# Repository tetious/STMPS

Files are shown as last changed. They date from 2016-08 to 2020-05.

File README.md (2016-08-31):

STMPS
=====

**STMPS** is a WIP 3d printer board based around the STM32f411, with inspiration and guidance
from the Printrboard, RAMPS 1.4, and the RepRap project.

**ALPHA-3**

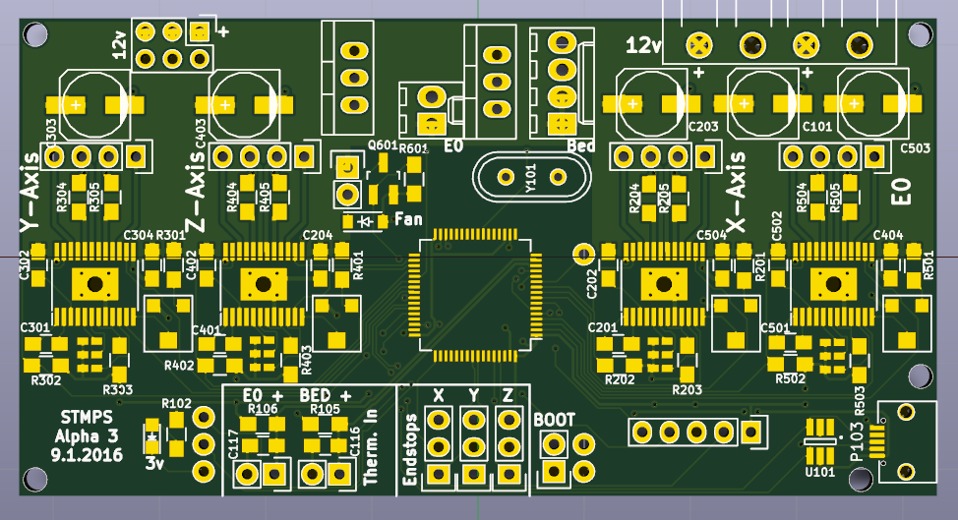
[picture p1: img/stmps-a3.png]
a3


This board is intended to work with Ambroz Bizjak's astonishingly fantastic 
[aprinter](https://github.com/ambrop72/aprinter) firmware. Configuration files and guidance will be
provided once the board is further along.

STMPS is open source hardware, licensed under CC BY-SA. Copyright (C) 2016 Greg Lincoln.

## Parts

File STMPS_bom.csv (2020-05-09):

Component | Description | Part | References | Value | Footprint | Quantity Per PCB | Datasheet | MPN
1 | Unpolarized capacitor | C_Small | C108 C110 C111 C112 C201 C202 C204 C301 C302 C304 C401 C402 C404 C501 C502 C504 | 100nf | C_0805_HandSoldering | 16
2 | Polarised capacitor | CP_Small | C101 | 100uf | c_elec_6.3x5.8 | 1 |  | 35TZV100M6.3X8
3 | Polarised capacitor | CP1_Small | C203 C303 C403 C503 | 100uf | c_elec_6.3x5.8 | 4 |  | UWT1V101MCL1GS
4 | Unpolarized capacitor | C_Small | C102 C116 C117 | 10uf | C_0805_HandSoldering | 3
5 | Unpolarized capacitor | C_Small | C103 C104 | 20pf | C_0805_HandSoldering | 2
6 | Unpolarized capacitor | C_Small | C113 C114 | 4.7uf | C_0805_HandSoldering | 2
7 | LED, small symbol | LED_Small | D101 | 12v_PWR | LED_0805 | 1
8 | LED, small symbol | LED_Small | D102 | 3v_PWR | LED_0805 | 1
9 | Schottky diode, small symbol | D_Schottky_Small | D103 D601 | D_Schottky_Small | SOD-123 | 2 |  | DB2X41100L DB2J41100L
10 | LED, small symbol | LED_Small | D701 D801 | r | LED_0805 | 2
11 | Connector, single row, 01x02, pin header | CONN_01X02 | JP101 | BOOT0 | Pin_Header_Straight_1x02 | 1
12 | Jumper, normally closed | Jumper_NC_Small | JP203 JP303 JP403 JP503 | MS1 | MADW__SMD-solder-bridge-narrow | 4
13 | Jumper, normally closed | Jumper_NC_Small | JP202 JP302 JP402 JP502 | MS2 | MADW__SMD-solder-bridge-narrow | 4
14 | Jumper, normally closed | Jumper_NC_Small | JP201 JP301 JP401 JP501 | MS3 | MADW__SMD-solder-bridge-narrow | 4
15 | Connector, double row, 02x03, pin header | CONN_02X03 | P102 | 12v | Pin_Header_Straight_2x03 | 1
16 | Connector, single row, 01x04, pin header | CONN_01X04 | P101 | 12v IN | 5EHDRC_1x04 | 1
17 | Connector, single row, 01x04, pin header | CONN_01X04 | P110 | BED | Molex_KK-6410-04_04x2.54mm_Straight | 1
18 | Connector, single row, 01x02, pin header | CONN_01X02 | P107 | BED_THERM | Pin_Header_Straight_1x02 | 1
19 | Connector, single row, 01x02, pin header | CONN_01X02 | P104 | E0_THERM | Pin_Header_Straight_1x02 | 1
20 | Connector, single row, 01x02, pin header | CONN_01X02 | P111 | EO | Molex_KK-6410-02_02x2.54mm_Straight | 1
21 | Connector, single row, 01x02, pin header | CONN_01X02 | P601 | LP_OUT | Pin_Header_Straight_1x02 | 1
22 | Connector, single row, 01x04, pin header | CONN_01X04 | P201 P301 P401 P501 | MOT | Pin_Header_Straight_1x04 | 4
23 | Connector, single row, 01x05, pin header | CONN_01X05 | P106 | SWD | Pin_Header_Straight_1x05 | 1
24 | USB mini/micro connector | USB_OTG | P103 | USB_OTG | USB_Micro-B-ebay | 1
25 | Connector, single row, 01x03, pin header | CONN_01X03 | P105 | X_STOP | Pin_Header_Straight_1x03 | 1
26 | Connector, single row, 01x03, pin header | CONN_01X03 | P108 | Y_STOP | Pin_Header_Straight_1x03 | 1
27 | Connector, single row, 01x03, pin header | CONN_01X03 | P109 | Z_STOP | Pin_Header_Straight_1x03 | 1
28 | Transistor N-MOSFET with substrate diode (general) | Q_NMOS_GDS | Q701 Q801 | IPP039N04L | TO-220_Neutral123_Vertical | 2 |  | IPP039N04LGXKSA1-ND
29 | Transistor N-MOSFETwith substrate diode (general) | Q_NMOS_GSD | Q601 | SSM3K333 | SOT-23_Handsoldering | 1 |  | SSM3K333RLFCT-ND
30 | Resistor, small symbol | R_Small | R204 R205 R304 R305 R404 R405 R504 R505 | 0.1 | R_0805_HandSoldering | 8
31 | Resistor, small symbol | R_Small | R702 R802 | 100 | R_0805_HandSoldering | 2
32 | Resistor, small symbol | R_Small | R104 R202 R203 R302 R303 R402 R403 R502 R503 R601 R701 R801 | 100k | R_0805_HandSoldering | 12
33 | Resistor, small symbol | R_Small | R201 R301 R401 R501 | 200k | R_0805_HandSoldering | 4
34 | Resistor, small symbol | R_Small | R103 | 220 | R_0805_HandSoldering | 1
35 | Resistor, small symbol | R_Small | R105 R106 R107 | 4.7k | R_0805_HandSoldering | 3
36 | Resistor, small symbol | R_Small | R102 | 56 | R_0805_HandSoldering | 1
37 | Resistor, small symbol | R_Small | R101 R703 R803 | 560 | R_0805_HandSoldering | 3
38 | Potentionmeter | POT | RV201 RV301 RV401 RV501 | 100k | BOURNS-TC33X-2 | 4 |  | TC33X-2-104E
39 |  | A5984 | U201 U301 U401 U501 | A5984 | TSSOP-24_4.4x7.8mm_Pitch0.65mm | 4 |  | A5984GLPTR-T
40 |  | AOZ8904 | U101 | AOZ8904 | SOT-23-6_Handsoldering | 1 |  | AOZ8904CIL
41 |  | CHIP-TOP | U105 | CHIP-TOP | CHIP-MIN | 1
42 |  | LM1117 | U102 | LM1117-3.3v | TO-252-2Lead | 1
43 |  | STM32F411RCTx | U103 | STM32F411RCTx | LQFP-64_10x10mm_Pitch0.5mm | 1 |  | STM32F411RCT6
44 | Two pin crystal, small symbol | Crystal_Small | Y101 | Crystal | Crystal_HC49-U_Vertical | 1 |  | ABL-8.000MHZ-B2
Component Groups: | 44
Component Count: | 113
Fitted Components: | 113
Number of PCBs: | 1
Total components: | 113
Schematic Version:
Schematic Date:
BoM Date: | Thu 20 Jul 2017 09:48:18 PM EDT
Schematic Source: | /home/greg/Boards/STMPS/STMPS.sch
KiCad Version: | Eeschema 4.0.7-e0-6372~58~ubuntu16.04.1

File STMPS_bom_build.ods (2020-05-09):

Part | References | Value | MPN
C_Small | C108 C110 C111 C112 C201 C202 C204 C301 C302 C304 C401 C402 C404 C501 C502 C504 | 100nf
CP_Small | C101 | 100uf | 35TZV100M6.3X8
CP1_Small | C203 C303 C403 C503 | 100uf | UWT1V101MCL1GS
C_Small | C102 C116 C117 | 10uf
C_Small | C103 C104 | 20pf
C_Small | C113 C114 | 4.7uf
LED_Small | D101 | 12v_PWR
LED_Small | D102 | 3v_PWR
D_Schottky_Small | D103 D601 | D_Schottky_Small | DB2X41100L DB2J41100L
LED_Small | D701 D801 | r
CONN_01X02 | JP101 | BOOT0
Jumper_NC_Small | JP203 JP303 JP403 JP503 | MS1
Jumper_NC_Small | JP202 JP302 JP402 JP502 | MS2
Jumper_NC_Small | JP201 JP301 JP401 JP501 | MS3
CONN_02X03 | P102 | 12v
CONN_01X04 | P101 | 12v IN
CONN_01X04 | P110 | BED
CONN_01X02 | P107 | BED_THERM
CONN_01X02 | P104 | E0_THERM
CONN_01X02 | P111 | EO
CONN_01X02 | P601 | LP_OUT
CONN_01X04 | P201 P301 P401 P501 | MOT
CONN_01X05 | P106 | SWD
USB_OTG | P103 | USB_OTG
CONN_01X03 | P105 | X_STOP
CONN_01X03 | P108 | Y_STOP
CONN_01X03 | P109 | Z_STOP
Q_NMOS_GDS | Q701 Q801 | IPP039N04L | IPP039N04LGXKSA1-ND
Q_NMOS_GSD | Q601 | SSM3K333 | SSM3K333RLFCT-ND
R_Small | R204 R205 R304 R305 R404 R405 R504 R505 | 0.1
R_Small | R702 R802 | 100
R_Small | R104 R202 R203 R302 R303 R402 R403 R502 R503 R601 R701 R801 | 100k
R_Small | R201 R301 R401 R501 | 200k
R_Small | R103 | 220
R_Small | R105 R106 R107 | 4.7k
R_Small | R102 | 56
R_Small | R101 R703 R803 | 560
POT | RV201 RV301 RV401 RV501 | 100k | TC33X-2-104E
A5984 | U201 U301 U401 U501 | A5984 | A5984GLPTR-T
AOZ8904 | U101 | AOZ8904 | AOZ8904CIL
CHIP-TOP | U105 | CHIP-TOP
LM1117 | U102 | LM1117-3.3v
STM32F411RCTx | U103 | STM32F411RCTx | STM32F411RCT6
Crystal_Small | Y101 | Crystal | ABL-8.000MHZ-B2

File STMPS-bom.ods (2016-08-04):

Reference | Quantity | Value | Footprint | MPN
C101 C203 C303 C403 C503 | 5 | 100uf | Capacitors_SMD:c_elec_6.3x5.8 | 35TZV100M6.3X8
C102 C116 C117 | 3 | 10uf | Capacitors_SMD:C_0805_HandSoldering
C103 C104 | 2 | 20pf | Capacitors_SMD:C_0805_HandSoldering
C109 | 1 | 1uf | Capacitors_SMD:C_0805_HandSoldering
C113 C114 | 2 | 4.7uf | Capacitors_SMD:C_0805_HandSoldering
C118 C201 C202 C204 C301 C302 C304 C401 C402 C404 C501 C502 C504 C105 C106 C107 C108 C110 C111 C112 | 20 | 0.1uf | Capacitors_SMD:C_0805_HandSoldering
D101 | 1 | 12v_PWR | LEDs:LED_0805
D102 | 1 | 3v_PWR | LEDs:LED_0805
D601 | 1 | D_Schottky_Small | Diodes_SMD:SOD-123 | DB2J41100L | DB2X41100L
D701 D801 | 2 | r | LEDs:LED_0805
P101 | 1 | 12v IN | stmps:5EHDRC_1x04 |  | Tayda
P102 | 1 | 12v | Pin_Headers:Pin_Header_Straight_2x03 |  | Tayda
P103 | 1 | USB_OTG | Connect:USB_Micro-B
P104 | 1 | E0_THERM | Pin_Headers:Pin_Header_Straight_1x02 |  | Tayda
P105 | 1 | X_STOP | Pin_Headers:Pin_Header_Straight_1x03 |  | Tayda
P106 | 1 | SWD | Pin_Headers:Pin_Header_Straight_1x06 |  | Tayda
P107 | 1 | BED_THERM | Pin_Headers:Pin_Header_Straight_1x02 |  | Tayda
P108 | 1 | Y_STOP | Pin_Headers:Pin_Header_Straight_1x03 |  | Tayda
P109 | 1 | Z_STOP | Pin_Headers:Pin_Header_Straight_1x03 |  | Tayda
P201 P301 P401 P501 | 4 | MOT | Pin_Headers:Pin_Header_Straight_1x04 |  | Tayda
P601 | 1 | LP_OUT | Pin_Headers:Pin_Header_Straight_1x02 |  | Tayda
P701 P801 | 2 | OUT | Connectors_Molex:Molex_KK-6410-02_02x2.54mm_Straight |  | Tayda
Q601 | 1 | SSM3K333 | TO_SOT_Packages_SMD:SOT-23_Handsoldering | SSM3K333RLFCT-ND
Q701 Q801 | 2 | IPP039N04L | TO_SOT_Packages_THT:TO-220_Neutral123_Vertical | IPP039N04LGXKSA1-ND | Tayda
R101 R703 R803 | 3 | 560 | Resistors_SMD:R_0805_HandSoldering
R102 | 1 | 56 | Resistors_SMD:R_0805_HandSoldering
R103 | 1 | 220 | Resistors_SMD:R_0805_HandSoldering
R104 R202 R203 R302 R303 R402 R403 R502 R503 R601 R701 R801 | 12 | 100k | Resistors_SMD:R_0805_HandSoldering
R105 R106 R107 R108 | 4 | 4.7k | Resistors_SMD:R_0805_HandSoldering
R201 R301 R401 R501 | 4 | 200k | Resistors_SMD:R_0805_HandSoldering
R204 R205 R304 R305 R404 R405 R504 R505 | 8 | 0.1 | Resistors_SMD:R_0805_HandSoldering
R702 R802 | 2 | 100 | Resistors_SMD:R_0805_HandSoldering
RV201 RV301 RV401 RV501 | 4 | 100k | stmps:BOURNS-TC33X-2 | TC33X-2-104E
U101 | 1 | AOZ8904 | TO_SOT_Packages_SMD:SOT-23-6_Handsoldering | AOZ8904CIL
U102 | 1 | LM1117-3.3v | TO_SOT_Packages_SMD:TO-252-2Lead
U103 | 1 | STM32F411RCTx | Housings_QFP:LQFP-64_10x10mm_Pitch0.5mm | STM32F411RCT6 | Future
U104 | 1 | M24C04 | Housings_SOIC:SOIC-8_3.9x4.9mm_Pitch1.27mm | M24C04-WMN6TP
U201 U301 U401 U501 | 4 | A5984 | stmps:TSSOP-24_4.4x7.8mm_Pitch0.65mm | A5984GLPTR-T
Y101 | 1 | Crystal | Crystals:Crystal_HC49-U_Vertical | ABL-8.000MHZ-B2 | Tayda

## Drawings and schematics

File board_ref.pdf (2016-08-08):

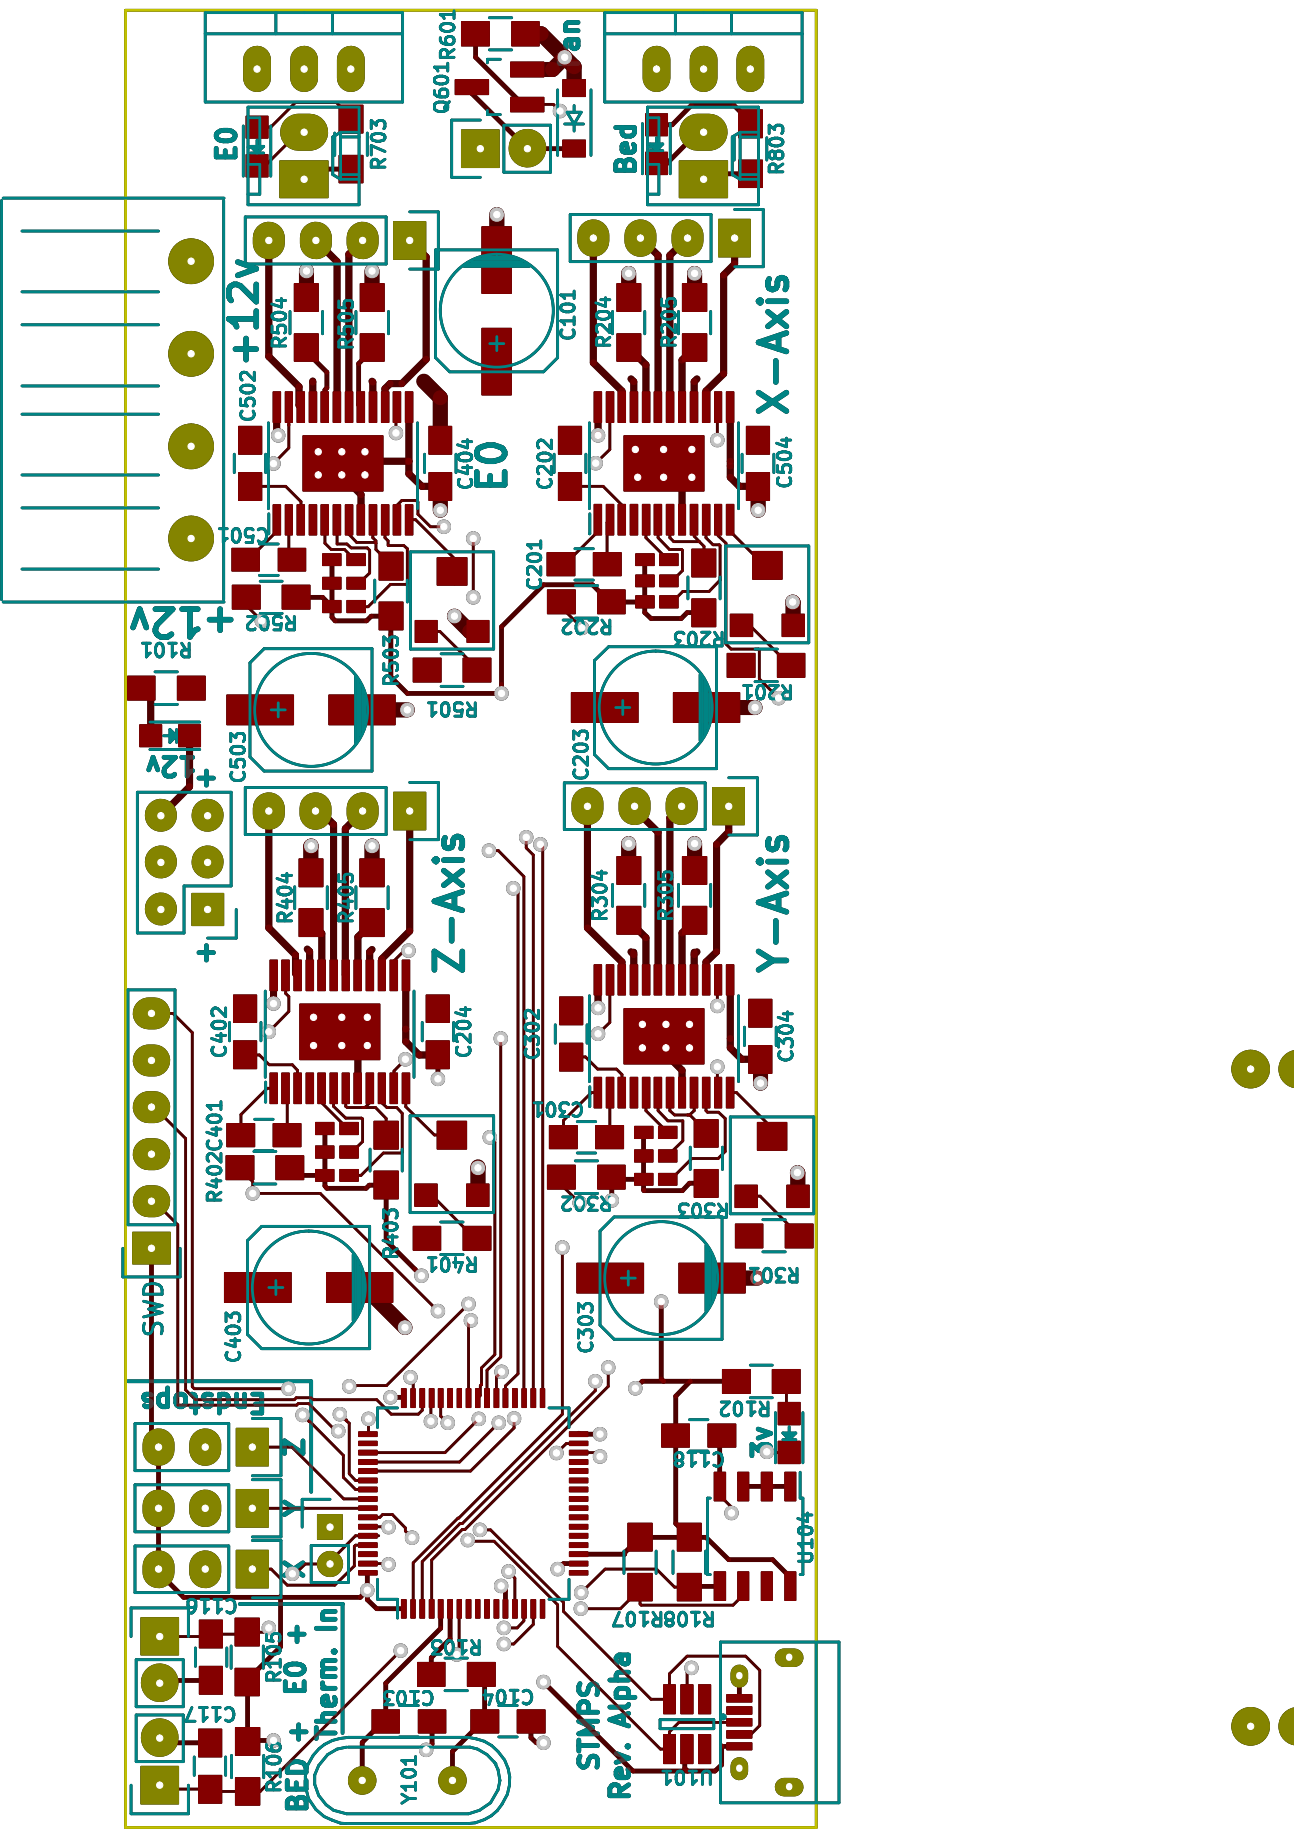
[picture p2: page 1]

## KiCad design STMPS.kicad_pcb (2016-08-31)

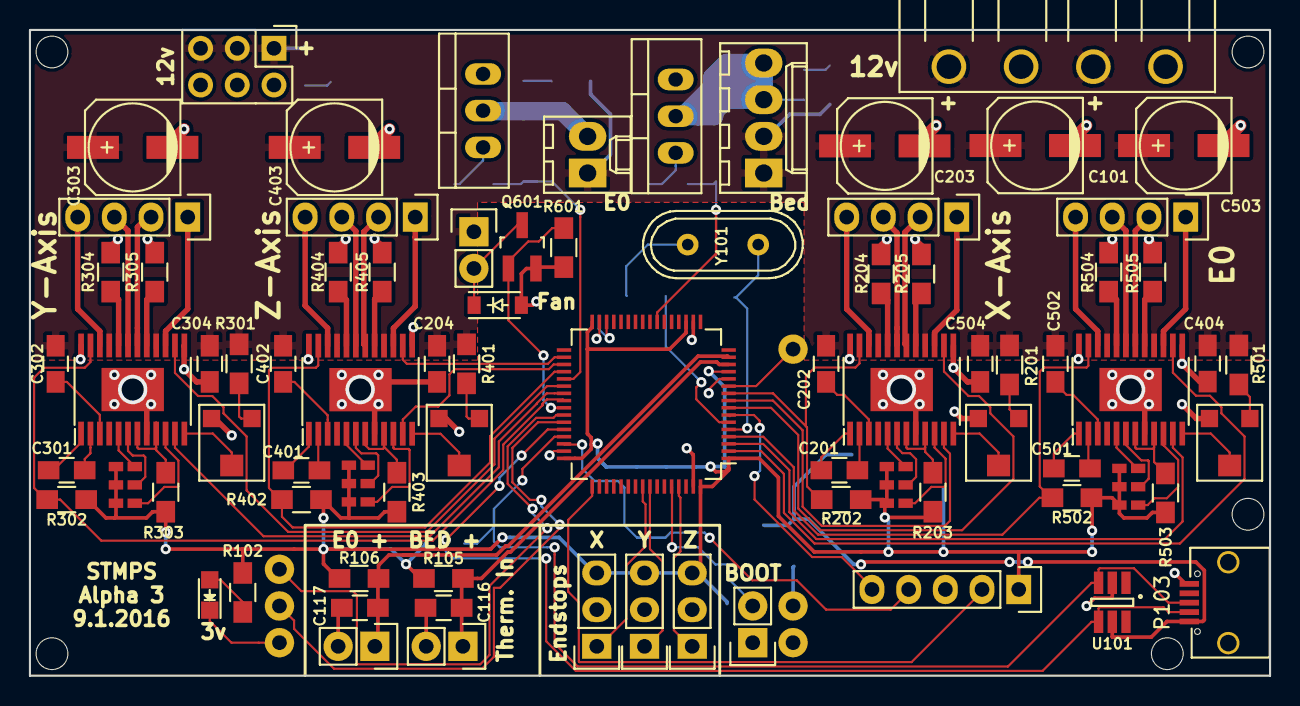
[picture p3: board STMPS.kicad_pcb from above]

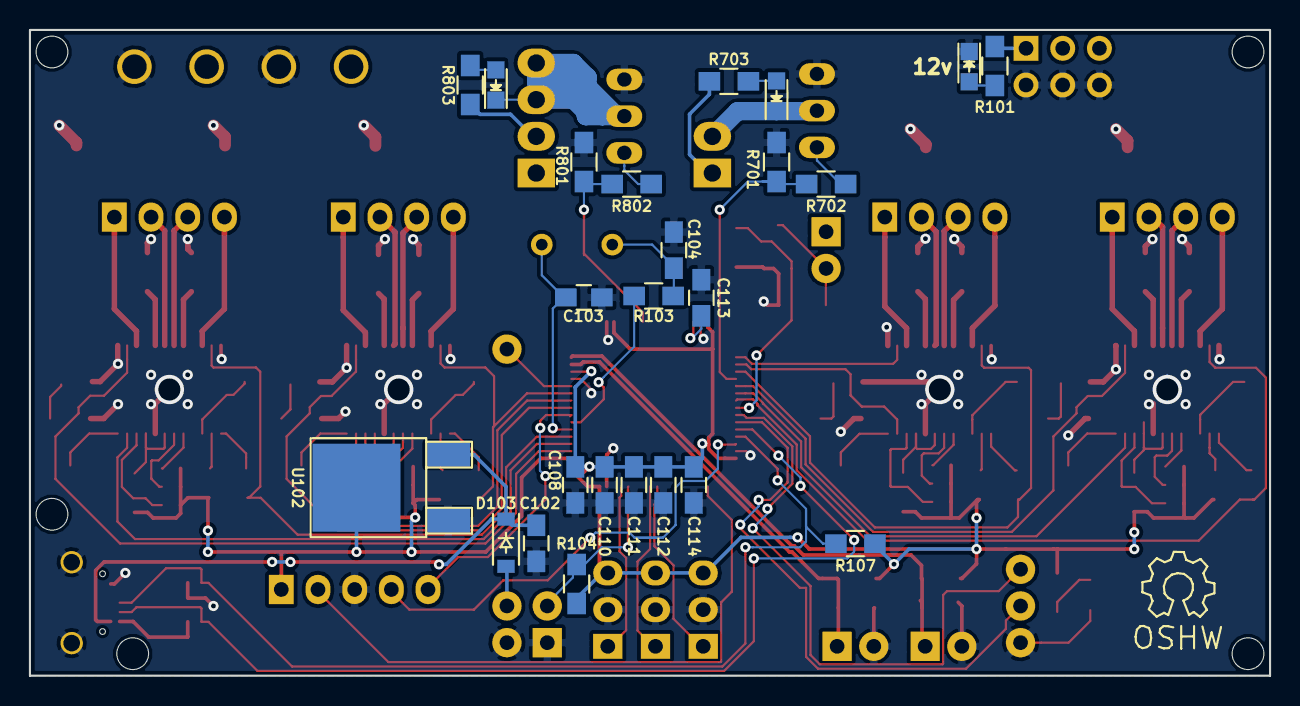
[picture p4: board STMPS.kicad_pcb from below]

Board: 2 copper layers, 85.9 x 44.7 mm, 113 parts (24 on the bottom side), 107 nets.

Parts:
C101, C203, C303, C403, C503: 100uf; c_elec_6.3x5.8
C102, C116, C117: 10uf; C_0805_HandSoldering
C103, C104: 20pf; C_0805_HandSoldering
C108, C110, C111, C112: 100nf; C_0805_HandSoldering
C113, C114: 4.7uf; C_0805_HandSoldering
C201, C202, C204, C301, C302, C304, C401, C402, C404, C501, C502, C504: 0.1uf; C_0805_HandSoldering
D101: 12v_PWR; LED_0805
D102: 3v_PWR; LED_0805
D103, D601: D_Schottky_Small; SOD-123
D701, D801: r; LED_0805
JP101: BOOT0; Pin_Header_Straight_1x02
JP201, JP301, JP401, JP501: MS3; MADW__SMD-solder-bridge-narrow
JP202, JP302, JP402, JP502: MS2; MADW__SMD-solder-bridge-narrow
JP203, JP303, JP403, JP503: MS1; MADW__SMD-solder-bridge-narrow
P101: 12v IN; 5EHDRC_1x04
P102: 12v; Pin_Header_Straight_2x03
P103: USB_OTG; USB_Micro-B-ebay
P104: E0_THERM; Pin_Header_Straight_1x02
P105: X_STOP; Pin_Header_Straight_1x03
P106: SWD; Pin_Header_Straight_1x05
P107: BED_THERM; Pin_Header_Straight_1x02
P108: Y_STOP; Pin_Header_Straight_1x03
P109: Z_STOP; Pin_Header_Straight_1x03
P110: BED; Molex_KK-6410-04_04x2.54mm_Straight
P111: EO; Molex_KK-6410-02_02x2.54mm_Straight
P201, P301, P401, P501: MOT; Pin_Header_Straight_1x04
P601: LP_OUT; Pin_Header_Straight_1x02
Q601: SSM3K333; SOT-23_Handsoldering
Q701, Q801: IPP039N04L; TO-220_Neutral123_Vertical
R101, R703, R803: 560; R_0805_HandSoldering
R102: 56; R_0805_HandSoldering
R103: 220; R_0805_HandSoldering
R104, R202, R203, R302, R303, R402, R403, R502, R503, R601, R701, R801: 100k; R_0805_HandSoldering
R105, R106, R107: 4.7k; R_0805_HandSoldering
R201, R301, R401, R501: 200k; R_0805_HandSoldering
R204, R205, R304, R305, R404, R405, R504, R505: 0.1; R_0805_HandSoldering
R702, R802: 100; R_0805_HandSoldering
RV201, RV301, RV401, RV501: 100k; BOURNS-TC33X-2
U101: AOZ8904; SOT-23-6_Handsoldering
U102: LM1117-3.3v; TO-252-2Lead
U103: STM32F411RCTx; LQFP-64_10x10mm_Pitch0.5mm
U105: CHIP-TOP; CHIP-MIN
U201, U301, U401, U501: A5984; TSSOP-24_4.4x7.8mm_Pitch0.65mm
Y101: Crystal; Crystal_HC49-U_Vertical

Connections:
+3.3v: C108.1, C110.1, C111.1, C112.1, C114.1, JP201.1, JP202.1, JP203.1, JP301.1, JP302.1, JP303.1, JP401.1, JP402.1, JP403.1, JP501.1, JP502.1, JP503.1, P105.3, P106.1, P108.3, P109.3, R102.2, R104.2, R105.1, R106.1, R107.1, R202.2, R203.2, R302.2, R303.2, R402.2, R403.2, R502.2, R503.2, U102.2, U103.1, U103.13, U103.19, U103.32, U103.48, U103.64
+12v: C101.1, C202.2, C203.1, C204.1, C302.2, C303.1, C304.1, C402.2, C403.1, C404.1, C502.2, C503.1, C504.1, P101.1, P101.3, P102.1, P102.3, P102.5, P110.1, P110.2, P111.1, P601.1, R101.2, R201.2, R301.2, R401.2, R501.2, R703.2, R803.2, U201.16, U201.21, U301.16, U301.21, U401.16, U401.21, U501.16, U501.21
/+5v: C102.1, D103.1, P103.1, U101.5, U102.3
/BED_FET/OUT-: D801.1, P110.3, P110.4, Q801.2
/BED_PWM: R801.1, R802.2, U103.23
/BED_THERM: C117.2, P107.1, R106.2, U103.15
/CHIP_1_WIRE: U103.11, U105.17
/E0_DIR: U103.2, U501.14
/E0_ENABLE: R502.1, U103.4, U501.23
/E0_FET/OUT-: D701.1, P111.2, Q701.2
/E0_PWM: R701.1, R702.2, U103.37
/E0_STEP: U103.3, U501.11
/E0_THERM: C116.2, P104.1, R105.2, U103.14
/FAN_PWM: Q601.1, R601.1, U103.41
/NRST: P106.5, U103.7
/SWCLK: P106.2, U103.49
/SWDIO: P106.4, U103.46
/USART1_RX: U103.43, U105.43
/USART1_TX: U103.42, U105.45
/USB_DM: P103.2, U101.4, U103.44
/USB_DP: P103.3, R107.2, U101.3, U103.45
/X_DIR: U103.8, U201.14
/X_ENABLE: R202.1, U103.10, U201.23
/X_STEP: U103.9, U201.11
/X_STOP: P105.1, U103.56
/Y_DIR: U103.38, U301.14
/Y_ENABLE: R302.1, U103.40, U301.23
/Y_STEP: U103.39, U301.11
/Y_STOP: P108.1, U103.57
/Z_DIR: U103.34, U401.14
/Z_ENABLE: R402.1, U103.36, U401.23
/Z_STEP: U103.35, U401.11
/Z_STOP: P109.1, U103.61
GND: C101.2, C102.2, C103.2, C104.2, C108.2, C110.2, C111.2, C112.2, C113.2, C114.2, C116.1, C117.1, C203.2, C204.2, C303.2, C304.2, C403.2, C404.2, C503.2, C504.2, D101.1, D102.1, D601.2, JP101.1, P101.2, P101.4, P102.2, P102.4, P102.6, P103.5, P103.6, P104.2, P105.2, P106.3, P107.2, P108.2, P109.2, Q601.2, Q701.3, Q801.3, R204.2, R205.2, R304.2, R305.2, R404.2, R405.2, R504.2, R505.2, R601.2, R701.2, R801.2, RV201.3, RV301.3, RV401.3, RV501.3, U101.2, U102.1, U103.12, U103.18, U103.31, U103.47, U103.63, U105.1, U105.41, U201.8, U201.13, U201.24, U201.T, U301.8, U301.13, U301.24, U301.T, U401.8, U401.13, U401.24, U401.T, U501.8, U501.13, U501.24, U501.T
unnamed: C103.1, U103.5, Y101.1
unnamed: C104.1, R103.2, Y101.2
unnamed: C113.1, U103.30
unnamed: C201.1, U201.1
unnamed: C201.2, U201.2
unnamed: C202.1, U201.3
unnamed: C301.1, U301.1
unnamed: C301.2, U301.2
unnamed: C302.1, U301.3
unnamed: C401.1, U401.1
unnamed: C401.2, U401.2
unnamed: C402.1, U401.3
unnamed: C501.1, U501.1
unnamed: C501.2, U501.2
unnamed: C502.1, U501.3
unnamed: D101.2, R101.1
unnamed: D102.2, R102.1
unnamed: D103.2, U105.3
unnamed: D601.1, P601.2, Q601.3
unnamed: D701.2, R703.1
unnamed: D801.2, R803.1
unnamed: JP101.2, R104.1, U103.60
unnamed: JP201.2, U201.10
unnamed: JP202.2, U201.6
unnamed: JP203.2, U201.5
unnamed: JP301.2, U301.10
unnamed: JP302.2, U301.6
unnamed: JP303.2, U301.5
unnamed: JP401.2, U401.10
unnamed: JP402.2, U401.6
unnamed: JP403.2, U401.5
unnamed: JP501.2, U501.10
unnamed: JP502.2, U501.6
unnamed: JP503.2, U501.5
unnamed: P201.1, U201.15
unnamed: P201.2, U201.18
unnamed: P201.3, U201.19
unnamed: P201.4, U201.22
unnamed: P301.1, U301.15
unnamed: P301.2, U301.18
unnamed: P301.3, U301.19
unnamed: P301.4, U301.22
unnamed: P401.1, U401.15
unnamed: P401.2, U401.18
unnamed: P401.3, U401.19
unnamed: P401.4, U401.22
unnamed: P501.1, U501.15
unnamed: P501.2, U501.18
unnamed: P501.3, U501.19
unnamed: P501.4, U501.22
unnamed: Q701.1, R702.1
unnamed: Q801.1, R802.1
unnamed: R103.1, U103.6
unnamed: R201.1, RV201.1
unnamed: R203.1, U201.7, U201.9
unnamed: R204.1, U201.20
unnamed: R205.1, U201.17
unnamed: R301.1, RV301.1
unnamed: R303.1, U301.7, U301.9
unnamed: R304.1, U301.20
unnamed: R305.1, U301.17
unnamed: R401.1, RV401.1
unnamed: R403.1, U401.7, U401.9
unnamed: R404.1, U401.20
unnamed: R405.1, U401.17
unnamed: R501.1, RV501.1
unnamed: R503.1, U501.7, U501.9
unnamed: R504.1, U501.20
unnamed: R505.1, U501.17
unnamed: RV201.2, U201.12
unnamed: RV301.2, U301.12
unnamed: RV401.2, U401.12
unnamed: RV501.2, U501.12

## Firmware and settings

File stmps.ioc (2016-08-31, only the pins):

Mcu.UserName=STM32F411RCTx
PA0-WKUP.Signal=ADCx_IN0
PA1.Signal=ADCx_IN1
PA10.Signal=USART1_RX
PA11.Signal=USB_OTG_FS_DM
PA12.Signal=USB_OTG_FS_DP
PA13.Signal=SYS_JTMS-SWDIO
PA14.Signal=SYS_JTCK-SWCLK
PA2.Signal=ADCx_IN2
PA3.Signal=ADCx_IN3
PA4.Signal=ADCx_IN4
PA5.Signal=ADCx_IN5
PA8.Signal=GPIO_Output
PA9.Signal=USART1_TX
PB10.Signal=SPI2_SCK
PB12.Signal=GPIO_Output
PB13.Signal=GPIO_Output
PB14.Signal=GPIO_Output
PB15.Signal=SPI2_MOSI
PB4.Signal=GPIO_Input
PB5.Signal=GPIO_Input
PB6.Signal=I2C1_SCL
PB7.Signal=I2C1_SDA
PB8.Signal=GPIO_Input
PB9.Signal=GPXTI9
PC1.Signal=GPIO_Output
PC10.Signal=GPIO_Output
PC11.Signal=GPIO_Output
PC12.Signal=GPIO_Output
PC13-ANTI_TAMP.Signal=GPIO_Output
PC14-OSC32_IN.Signal=GPIO_Output
PC15-OSC32_OUT.Signal=GPIO_Output
PC2.Signal=SPI2_MISO
PC3.Signal=GPXTI3
PC6.Signal=GPIO_Output
PC7.Signal=GPIO_Output
PC8.Signal=GPIO_Output
PC9.Signal=GPIO_Output
PD2.Signal=GPIO_Output

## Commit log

2016-07-31 Initial checkin.
    [STMPS.kicad_pcb, STMPS.sch, a5984_stepper.sch]
2016-08-01 Possibly finished schematic.
    [STMPS.sch, a5984_stepper.sch, high_power_fet.sch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]
2016-08-01 Start working on footprint assignments.
    [STMPS.sch, a5984_stepper.sch, high_power_fet.sch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]
2016-08-02 Finish assigning footprints.
    [STMPS.sch, a5984_stepper.sch, high_power_fet.sch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]
2016-08-02 Fix jumper names for steppers. Start prepping for layout.
    [STMPS.kicad_pcb, a5984_stepper.sch]
2016-08-03 Complete routing, first pass.
    [STMPS.kicad_pcb, STMPS.sch, a5984_stepper.sch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]
2016-08-03 Cleanup silkscreen and other minor tweaks.
    [STMPS.kicad_pcb]
2016-08-04 Fixed incorrect clock configuration.
    [stmps.ioc]
2016-08-04 Corrected resistors and rail for vREF.
    [a5984_stepper.sch]
2016-08-04 Finalized layout for Alpha 1.
    [STMPS-bom.ods, STMPS.kicad_pcb, STMPS.sch]
2016-08-07 Fix USB connection. Cleanups.
    [STMPS.kicad_pcb, STMPS.sch, a5984_stepper.sch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]
2016-08-08 WIP rev B.
    [STMPS.kicad_pcb, STMPS.sch, a5984_stepper.sch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]
2016-08-08 Alpha 2 board layout.
    [STMPS.kicad_pcb, STMPS.sch, a5984_stepper.sch]
2016-08-14 Minor cleanups.
    [STMPS.kicad_pcb]
2016-08-24 Hopefully fix issue with mask/pour clearance.
    Correctly tie VREF+ to VCC.
    [STMPS.kicad_pcb, STMPS.sch, a5984_stepper.sch]
2016-08-31 Alpha 3. Fix solder mask clearance. Fix 3.3v not tied to ref+. Tweaks and cleanups.
    [STMPS.kicad_pcb, STMPS.sch, high_power_fet.sch]
2016-08-31 A few more tweaks.
    [STMPS.kicad_pcb]
2016-08-31 Add board image.
2020-05-09 Update stuff. ;)
    [STMPS.sch, STMPS_bom.csv, STMPS_bom_build.ods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]
